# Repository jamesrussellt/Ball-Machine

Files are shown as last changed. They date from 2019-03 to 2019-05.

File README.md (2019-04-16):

# Ball-Sorting-Machine
University of Bath - Final Year Mechanical Engineering Masters Project

For exhibition and educational purposes.

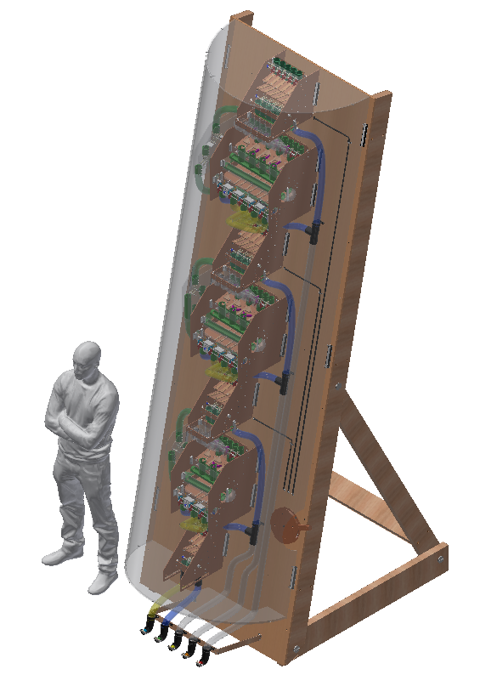
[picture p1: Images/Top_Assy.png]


## About this repository
As part of IMAGINARY open mathematics exhibitions (https://imaginary.org/), this machine demonstrates the use of Selection Sorting and Pancake Sorting Algorithms using balls of different weights.

## Selection Sorting Algorithm
This simple algorithm demonstrates the concept of sorting algorithms by least number of ball comparisons.

This algorithm picks the heaviest ball from the set of balls and places it to the right hand side of the pack. It will repeat this for the remaining balls until all balls have been sorted into weight order.

## Pancake Sorting Algorithm
This more complex algorithm demonstrates the concept of sorting algorithms by least number of reversals or 'flips'. You are more limited in this case than Selection Sort because you cannot simply pick the ball out of the pack and place it at the side.

Imagine you have a stack of pancakes of various sizes which you want in size order with the largest pancake (or heaviest ball in our case) at the bottom. You can only use your spatula to insert under the largest pancake and flip it, with any pancakes above it, so that the largest pancake rests on top of the pile. Then you re-insert your spatula at the bottom of the pile to flip all the pancakes at once so the largest pancake is now at the bottom of the pile. This method is repeated until all pancakes are in size order.

## How the machine works
The machine is effectively a repeat of a few sub assemblies which comprise the first line of the two algorithms. For each following line of both algorithms, the assemblies used are the same but adapted for one less ball lane.

A lever which can be seen towards the bottom right of the image above allows the user to switch between the two algorithms. For Selection Sort, the pancake comparator is skipped and the balls travel around it to the next selection comparator. For Pancake Sort, the balls travel straight from the selection comparator into the pancake comparator.

See `Pancake Sort` and `Selection Sort` for more information on how these comparators work to implement the two algorithms set out above.

## Contents

* `All Drawing PDFs`
  * All PDF manufacturing drawings for reference.
  * Drawings are also included in each sub-folder to show where they are used.
* `Top Level`
  * Machine full assembly.
  * Folder contains CAD models and manufacturing drawings.
* `Balls`
  * Balls of various weights required for the machine.
  * Folder contains CAD models and manufacturing drawings.
* `Pancake Sort`
  * Pancake Sort comparing mechanism.
  * Folder contains CAD models and manufacturing drawings.
* `Selection Sort`
  * Selection Sort comparing mechanism.
  * Folder contains CAD models and manufacturing drawings.
* `Timing Gate`
  * Timing Gate used for Selection Sort comparing mechanism.
  * Folder contains CAD models and manufacturing drawings.

The following folders were used for the creation of the machine and serve no purpose for manufacturing.

* `2018_Templates` 
  * Manufacturing drawing templates used when creating machine assembly and component drawings.
* `Images`
  * Images used for open source documentation.
* `Man`
  * CAD model of human used to present machine size.
* `OldVersions`
  * A backup of old overwritten files automatically saved when using Autodesk Inventor Software.
* `Prototype CAD`
  * A copy of the 'Selection Sort comparator' used to prove design principles.
  * Is built for larger 40mm balls and may contain other components for design adaptation.

## Manufacturing This Machine
Please see `BOM.xlsx` for full list of sub assemblies and parts required for this machine build.
Please see `All Drawing PDFs` for all manufacture drawings.

## Instructions 
See each folder for more detail.

## More info
Another comparing mechanism, designed by Evgeniy Shiryaev, can be used for sorting algorithms which require 2 balls to be compared at a time. This comparator was used as a starting point for the project and lead to the development of Selection and Pancake comparators which compare all balls at once.
See https://imaginary.org/hands-on/balls-sorting-mechanism

## Refer to this work
Cite as: James Taylor. (2019, March 28). jamesrussellt/Ball-Machine

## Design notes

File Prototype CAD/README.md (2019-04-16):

# Prototype CAD

A prototype of the `Selection Sort comparator` was made for demonstrating its design using larger 40mm balls.

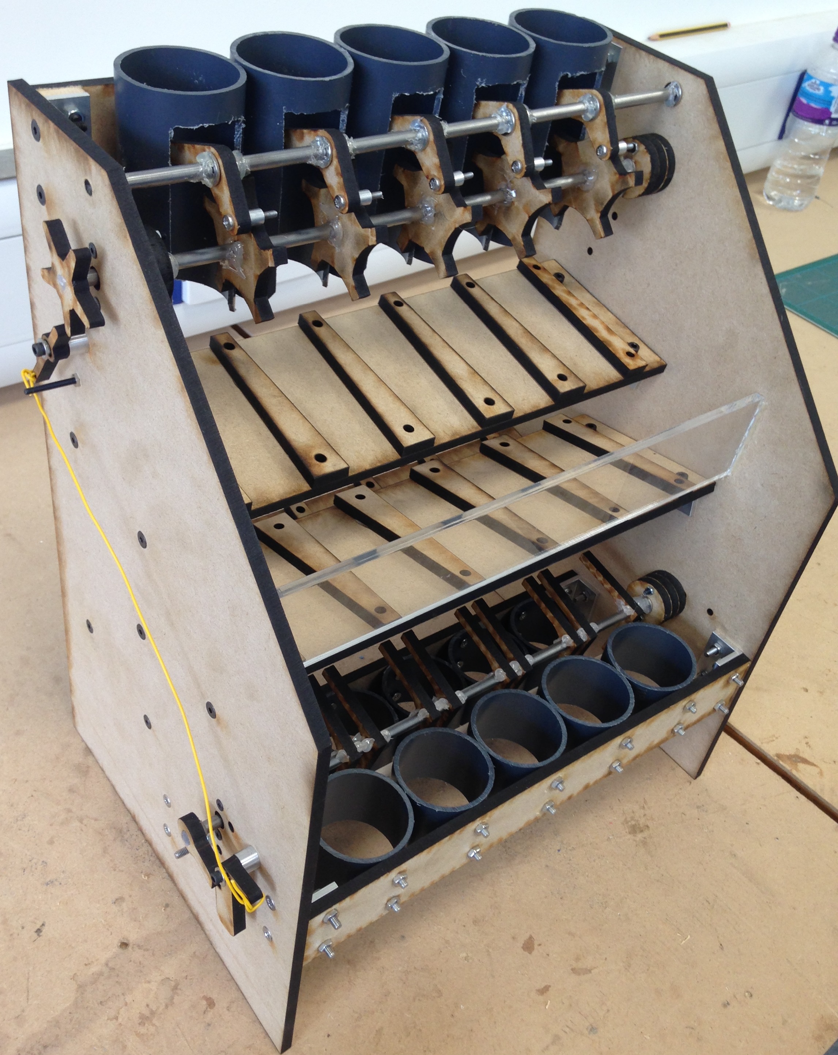
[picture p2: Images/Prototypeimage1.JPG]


Adaptations to the original design include:
 * A new `Star Piece` used in the `Timing Gate` assembly
 * A new `Reset Lever` used for holding and releasing the shaft used to separate the heaviest ball
 * A new `Ramp System` used for separating the heaviest ball from the rest

`Star Piece`
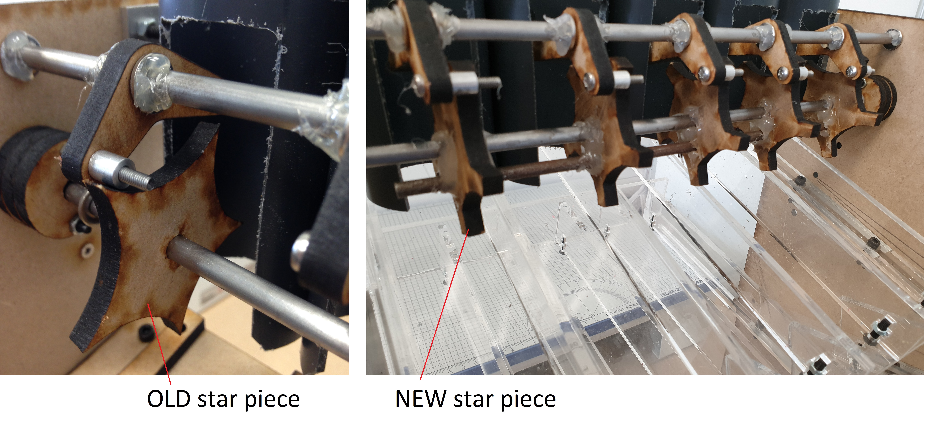
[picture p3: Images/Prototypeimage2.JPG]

 * Faces added to each point of star to prevent other lever slipping over it.

`Reset Lever`
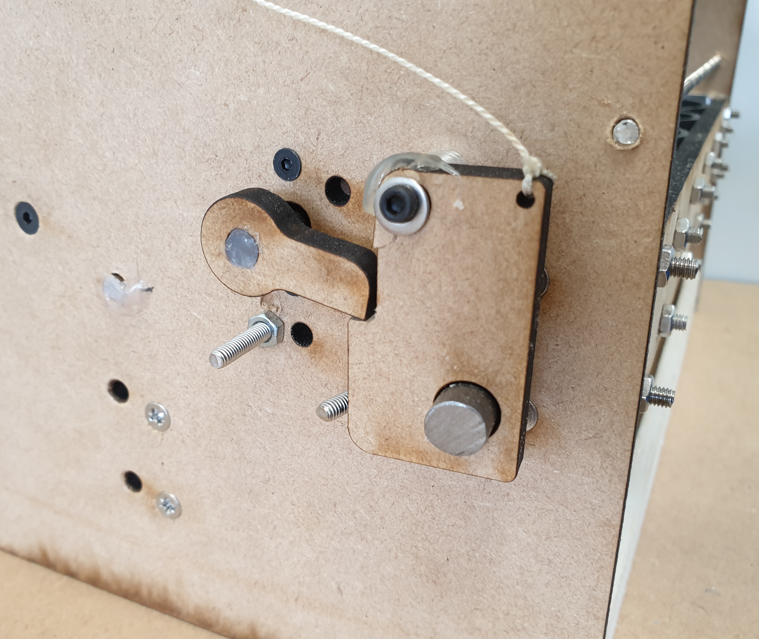
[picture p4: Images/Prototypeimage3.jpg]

 * Counter weight and stopper added to allow the lever to move into position faster when catching the shaft.
 * Please note lever was damaged in picture shown. Actual lever would not require glue to rest on shaft.

`Ramp System`
 * Old ramp system was proven by calculation and testing to not rely on ball weight but on ramp angle and friction. This design only works for balls of various surface roughnesses which may hinder starting speeds.
 * New ramp design required using individual rotating ramps per ball lane.
 * New ramp design has been calculated to require 3 rotating ramps of 150mm length each per ball lane.
 * This design will require further prototyping to prove its concept.

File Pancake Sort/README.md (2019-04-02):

# Pancake Sort

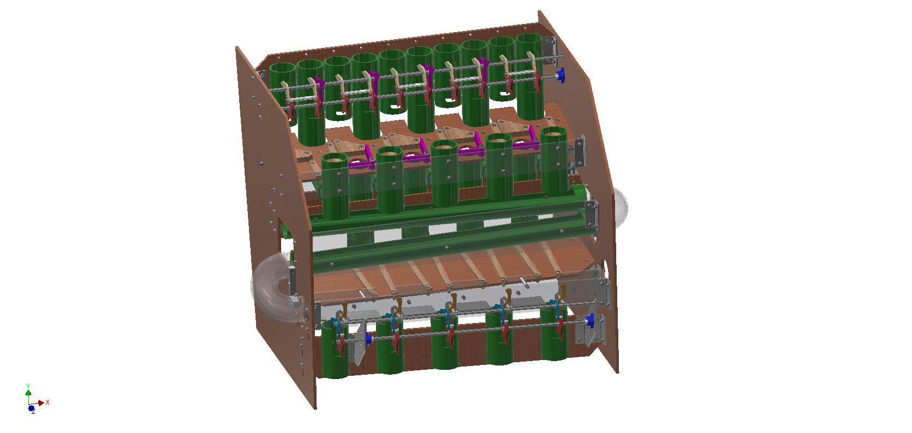
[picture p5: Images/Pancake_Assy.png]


This folder contains CAD models and drawings for the `Pancake Sort` comparator.

## How it works

This comparator uses the `Selection Sort` comparator before it to identify the heaviest ball and pass the balls into the corresponding `Pancake Sort` comparator entry tubes.

 * Each ball lane has two entry tubes (hence 10 entry tubes for 5 ball lanes) - Left for the lighter balls, Right for the heavier balls.

The `Pancake Sort` comparator flips the order of the heaviest ball and the balls to the left of it (just like flipping the largest pancake and all of the others on top of it). The balls to the right of the heaviest stay in lane. The tubes connecting the `Pancake Sort` comparator to the next line of the algorithm are connected so that the full sequence is flipped (the last stage of the Pancake Sort algorithm).

 * The heaviest ball hits a purple lever upon entry which changes the lane directions of the balls to the right of it.
 * These balls pass under the `Z` shaped ball run and into the exit timing gate.
 * The heaviest ball and the balls to the left pass into the `Z` shaped ball run.
 * This keeps the order of the balls the same as they pass into the exit timing gate.
 * The exit timing gate reverses the order of the entering balls as the first drops into place, the others pass over the top.
 * The balls are released out of the comparator at the same time for visual effect to watch the balls flip order as they pass through the connecting tubes (not shown in picture).

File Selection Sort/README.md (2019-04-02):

# Selection Sort

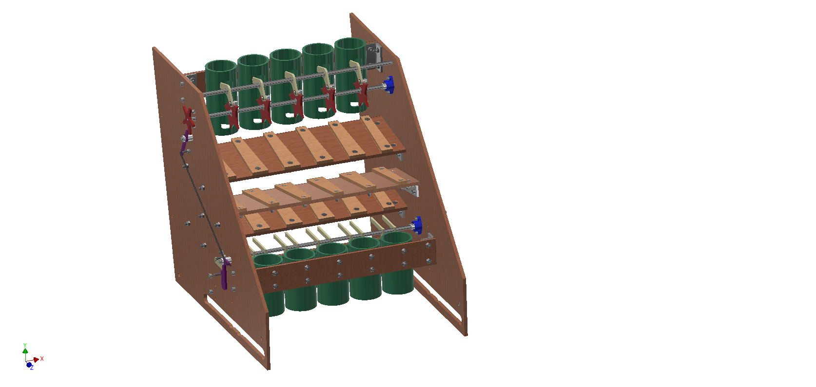
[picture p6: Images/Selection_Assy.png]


This folder contains the CAD models and manufacturing drawings required to make a selection sort comparator.

See folders `Selection - X Lanes` for copies of the design for the required number of ball lanes.

## How it works
The comparator is required to select and remove the heaviest ball as per the selection sort algorithm.

It comprises of 4 sections:
 * Timing Gate
 * Ramps
 * Selection Shaft
 * Reset mechanism
 
`Timing Gate`
 * To release all balls at the same time (see `Timing Gate` folder).
 
`Ramps`
* To allow the heaviest ball to roll to the bottom the quickest and separate it from the other balls (this design has been proven not to work and as such requires a design update and further prototyping work to complete - see `Prototype CAD` folder).
 
`Selection Shaft`
* The first ball down the ramps rotates the shaft and falls into the first set of tubes. The shaft is caught by a catch lever on the outer left hand side and the other balls roll over the top of the shaft into the other set of tubes. This separates the heaviest ball from the rest of the pack.

`Reset mechanism`
* For multiple uses of the machine, the reset mechanism releases the catch lever when the next set of balls pass the timing gate. A counterweight on the outer right hand side of the machine lifts the Selection shaft back into position.

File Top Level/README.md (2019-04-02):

# Top Level



This folder contains the full machine assembly using sub-assemblies from `Pancake Sort`, `Selection Sort` and `Timing Gate` along with manufacturing drawings.

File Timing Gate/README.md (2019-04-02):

# Timing Gate

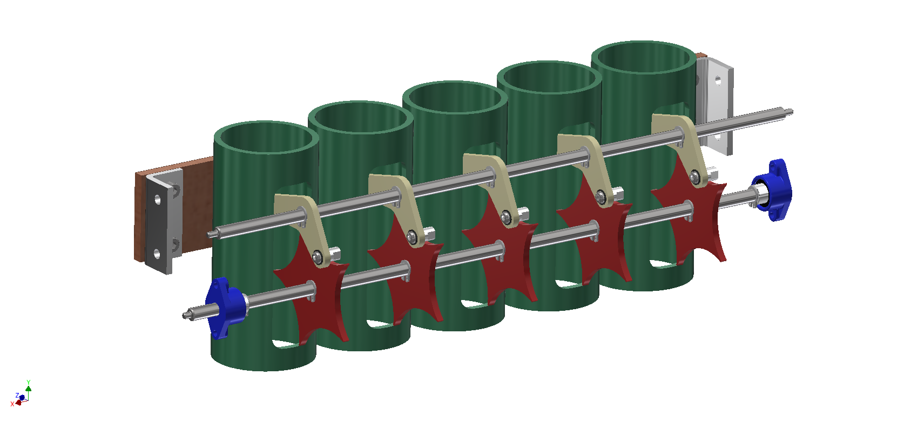
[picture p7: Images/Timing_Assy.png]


Used within `Selection Sort` comparator and adapated for the `Pancake Sort` comparator to release all balls at the same time once each ball arrives at the gate.

Each ball lifts the boomerange-shaped lever upon arrival which can rotate independantly on its shaft. Once all these levers are lifted, the star-shaped pieces, which are connected to the shaft so must rotate together, are free to rotate and the balls drop at the same time.

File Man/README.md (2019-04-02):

# Man

CAD model of human used to present machine size.

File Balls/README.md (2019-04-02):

# Balls

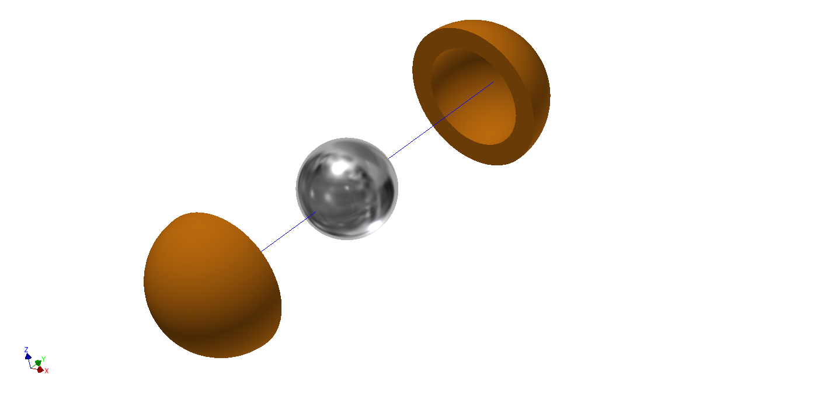
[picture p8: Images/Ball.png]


Contains models and drawings of balls to be used in machine.

Balls are made from steel ball bearings of various sizes incased in a 3D printed ABS plastic casing to ensure they all have the same outer diameter and surface roughness. The ball bearings are the main contributor in the weight difference between balls as steel has a high density of around 7700kg/m3.

The balls are manufactured from different coloured ABS plastic in the colours of the rainbow, i.e. red = heaviest ball -> blue = lightest ball. This allows people to see the balls sorted rather than having to compare weight differences by hand.

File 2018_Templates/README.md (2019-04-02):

# 2018_Templates

Manufacturing drawing templates used when creating machine assembly and component drawings (see image below).
Drawing template consists of premade borders and text boxes to increase productivity and consistency when creating part drawings.

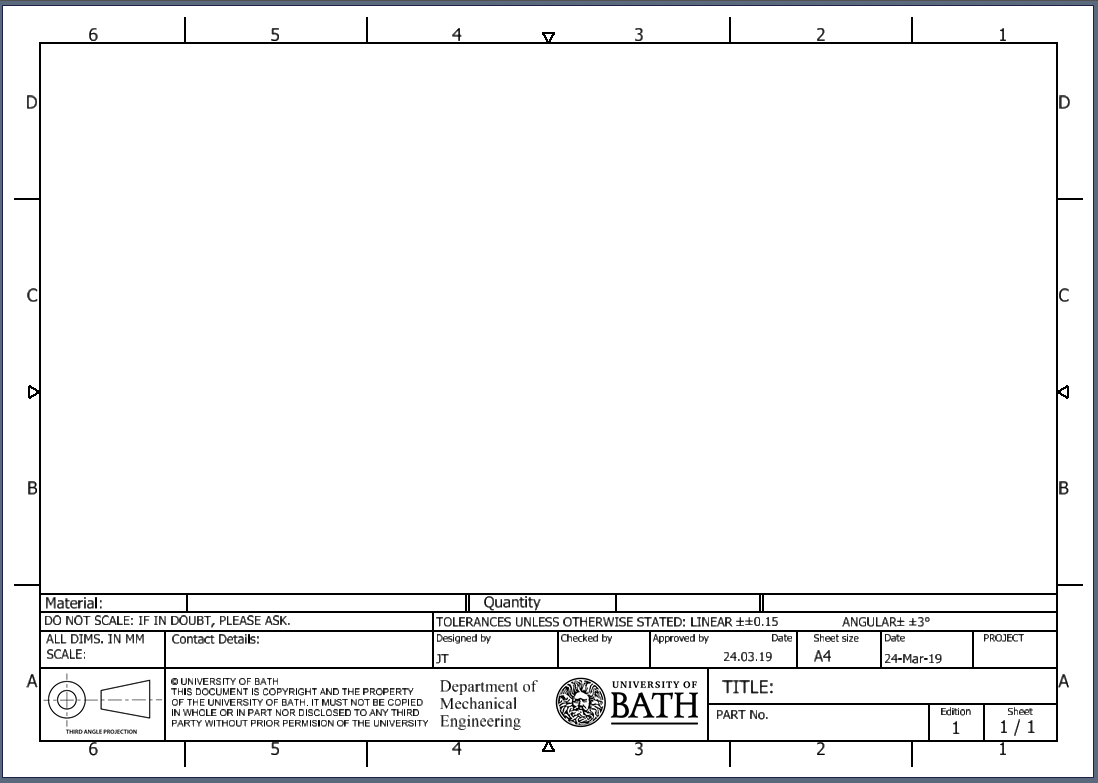
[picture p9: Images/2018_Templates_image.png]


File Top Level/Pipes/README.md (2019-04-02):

# Pipes

CAD models of all pipes used on `Top Level` assembly.

CAD models require multiple files for different pipe directions. In reality, flexible pipes will be cut from stock to length.

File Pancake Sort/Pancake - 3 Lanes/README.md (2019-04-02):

# Pancake Sort - 3 Lanes

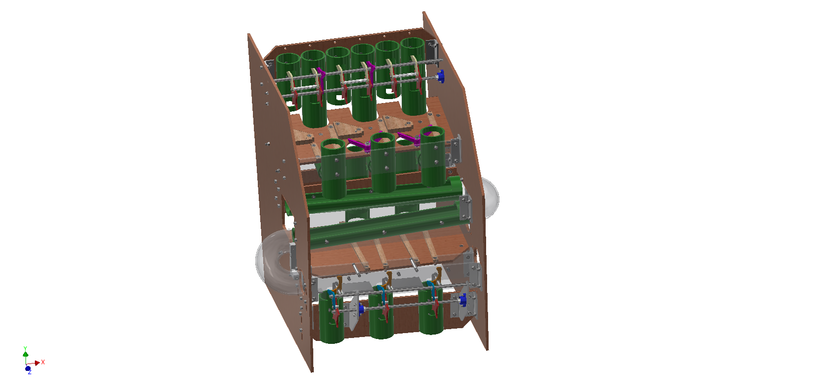
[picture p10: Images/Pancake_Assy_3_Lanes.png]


This folder is a copy of the Pancake Sort comparator design adapted for 3 ball lanes.

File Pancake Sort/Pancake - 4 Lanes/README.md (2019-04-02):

# Pancake Sort - 4 Lanes

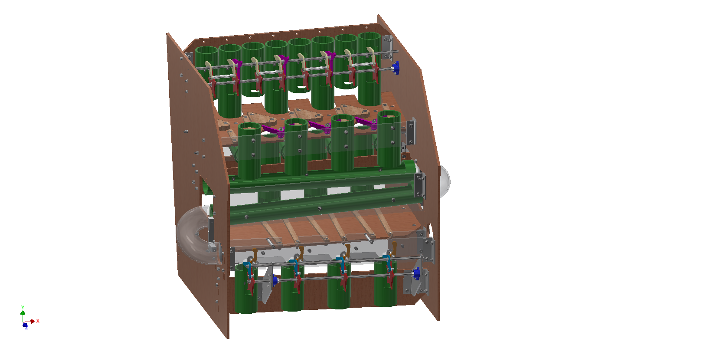
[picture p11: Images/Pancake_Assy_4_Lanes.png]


This folder is a copy of the Pancake Sort comparator design adapted for 4 ball lanes.

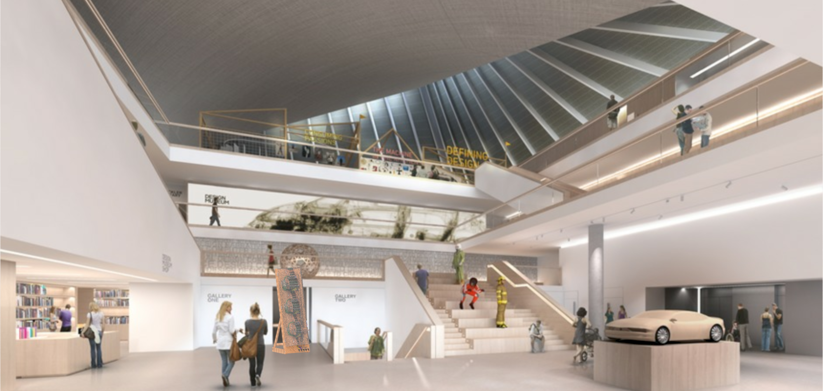
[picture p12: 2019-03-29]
Images/Top_Assy_Exhib_2.png

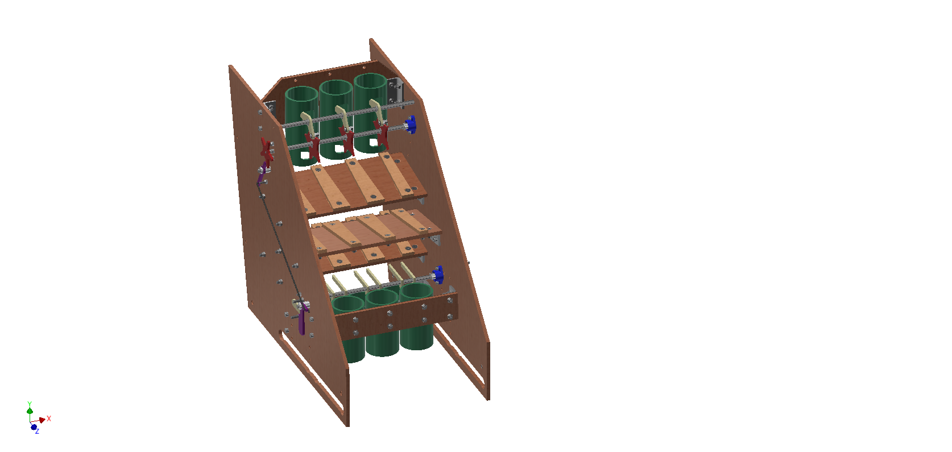
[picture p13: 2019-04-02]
Images/Selection_Assy_3_Lanes.png

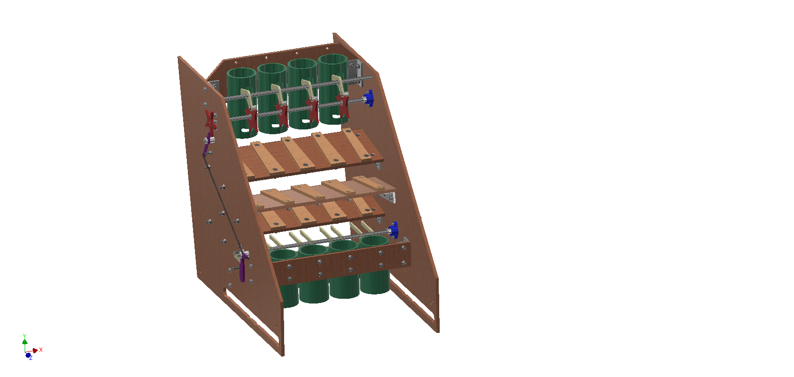
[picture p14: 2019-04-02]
Images/Selection_Assy_4_Lanes.png

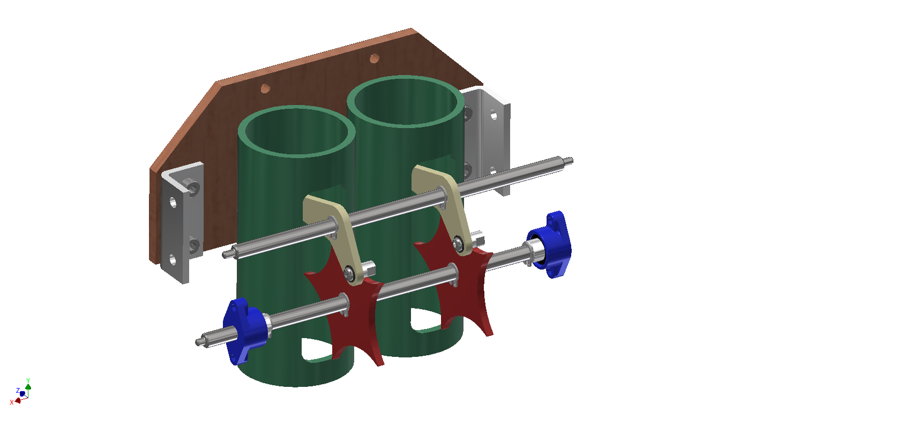
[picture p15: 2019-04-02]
Images/Timing_Assy_2_Lanes.png

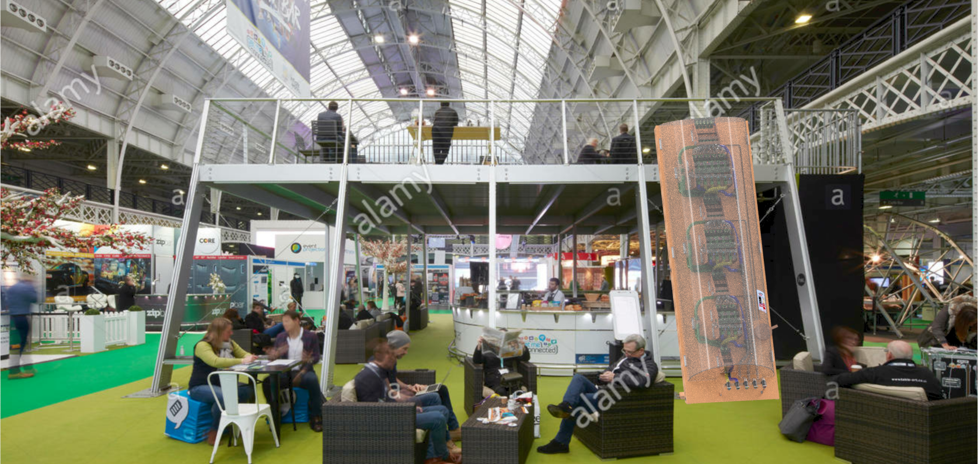
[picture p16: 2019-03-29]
Images/Top_Assy_Exhib_1.png

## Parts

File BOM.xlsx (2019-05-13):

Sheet: BOM
BOM
Top-Assy |  |  |  | Sub-Assy 1 |  |  |  | Sub-Assy 2 |  |  |  | Sub-Assy 3 |  |  |  | Sub-Assy 4
Part No. | Desc | Supplier | Qty | Part No. | Description | Supplier | Qty | Part No. | Description | Supplier | Qty | Part No. | Description | Supplier | Qty | Part No. | Description | Supplier | Qty
BSM.001.001 | Top_Assy | Workshop | 1 | 4082 | 42-50mm EPDM Adaptor | Plastic Pipe Shop | 34
 |  |  |  | 15528 | 40mm - 1 0.25inch Universal Plastic Pipe Clip c-w Spacer Block (PP) | Plastic Pipe Shop | 8
 |  |  |  | 16124 | 40mm Plain 90 Degree PVC Tee | Plastic Pipe Shop | 12
 |  |  |  | 450712010040016 | Socket Cap Screw - Standard - (A2) - M4 x 16 | TR Fastenings | 38
 |  |  |  | 450712010040025 | Socket Cap Screw - Standard - (A2) - M4 x 25 | TR Fastenings | 4
 |  |  |  | BSM.001.002 | Top_Backboard Assy | Workshop | 1 | 450712010040016 | Socket Cap Screw - Standard - (A2) - M4 x 16 | TR Fastenings | 52
 |  |  |  |  |  |  |  | 450712010040020 | Socket Cap Screw - Standard - (A2) - M4 x 20 | TR Fastenings | 12
 |  |  |  |  |  |  |  | 450712010040025 | Socket Cap Screw - Standard - (A2) - M4 x 25 | TR Fastenings | 40
 |  |  |  |  |  |  |  | 450712010080020 | Socket Cap Screw - Standard - (A2) - M8 x 20 | TR Fastenings | 6
 |  |  |  |  |  |  |  | BSM.001.103 | Top_Angle Bracket | Workshop | 26
 |  |  |  |  |  |  |  | BSM.001.104 | Top_Backboard | Workshop | 1
 |  |  |  |  |  |  |  | BSM.001.112 | Top_Floor Plank | Workshop | 2
 |  |  |  |  |  |  |  | BSM.001.116 | Top_Hinge Cylinder Long | Workshop | 2
 |  |  |  |  |  |  |  | BSM.001.117 | Top_Hinge Cylinder | Workshop | 4
 |  |  |  |  |  |  |  | BSM.001.118 | Top_Hinge End | Workshop | 6
 |  |  |  |  |  |  |  | BSM.001.126 | Top_Rear Plank_LHS | Workshop | 1
 |  |  |  |  |  |  |  | BSM.001.127 | Top_Rear Plank_RHS | Workshop | 1
 |  |  |  |  |  |  |  | BSM.001.128 | Top_Reinforcement 2 | Workshop | 3
 |  |  |  |  |  |  |  | BSM.001.129 | Top_Reinforcement 3 | Workshop | 1
 |  |  |  |  |  |  |  | BSM.001.130 | Top_Reinforcement_LHS | Workshop | 1
 |  |  |  |  |  |  |  | BSM.001.131 | Top_Reinforcement_RHS | Workshop | 1
 |  |  |  |  |  |  |  | BSM.001.148 | Top_Spacer | Workshop | 2
 |  |  |  |  |  |  |  | Din97 - 4x25 | Steel Wood Screw |  | 29
 |  |  |  |  |  |  |  | Din97 - 8x80 | Steel Wood Screw |  | 24
 |  |  |  |  |  |  |  | M4 - Nyloc Nut | Nyloc Nut - M4 | TR Fastenings | 92
 |  |  |  | BSM.001.003 | Top_Lever Assy | Workshop | 1 | 450712010080030 | Socket Cap Screw - Standard - (A2) - M8 x 30 | TR Fastenings | 1
 |  |  |  |  |  |  |  | BSM.001.119 | Top_Lever 2mm Spacer | Workshop | 1
 |  |  |  |  |  |  |  | BSM.001.120 | Top_Lever Cable Tie | Workshop | 6
 |  |  |  |  |  |  |  | BSM.001.121 | Top_Lever Centre | Workshop | 1
 |  |  |  |  |  |  |  | BSM.001.122 | Top_Lever End Piece | Workshop | 1
 |  |  |  |  |  |  |  | BSM.001.123 | Top_Lever Handle | Workshop | 1
 |  |  |  |  |  |  |  | BSM.001.124 | Top_Lever Shaft | Workshop | 1
 |  |  |  |  |  |  |  | BSM.001.125 | Top_Lever Side | Workshop | 2
 |  |  |  |  |  |  |  | Din97 - 4x12 | Steel Wood Screw |  | 18
 |  |  |  |  |  |  |  | M4 x 12 - Socket Csk Screw (A2) | Socket Csk Screw - (A2) - M4 x 12 | TR Fastenings | 1
 |  |  |  |  |  |  |  | PRB-256 | Standard Double Sealed Ball Bearing | SKF | 2
 |  |  |  | BSM.001.004 | Top_Separator Assy 2 Lanes | Workshop | 1 | 450712010040016 | Socket Cap Screw - Standard - (A2) - M4 x 16 | TR Fastenings | 4
 |  |  |  |  |  |  |  | 450712010040025 | Socket Cap Screw - Standard - (A2) - M4 x 25 | TR Fastenings | 4
 |  |  |  |  |  |  |  | BSM.001.103 | Top_Angle Bracket | Workshop | 2
 |  |  |  |  |  |  |  | BSM.001.132 | Top_Separator Backboard 2 Lanes | Workshop | 2
 |  |  |  |  |  |  |  | BSM.001.136 | Top_Separator Lever | Workshop | 2
 |  |  |  |  |  |  |  | BSM.001.138 | Top_Separator Pipe | Workshop | 3
 |  |  |  |  |  |  |  | BSM.001.139 | Top_Separator Shaft | Workshop | 1
 |  |  |  |  |  |  |  | BSM.001.140 | Top_Separator Weight 2 | Workshop | 2
 |  |  |  |  |  |  |  | BSM.001.141 | Top_Separator Weight | Workshop | 1
 |  |  |  |  |  |  |  | BSM.004.102 | Pancake_Bearing | Workshop | 2
 |  |  |  |  |  |  |  | circlip-6-bs-3673 | External Circlip |  | 2
 |  |  |  |  |  |  |  | M3 x 8 - Socket Cap Screw - Standard (A2) | Socket Cap Screw - Standard - (A2) - M3 x 8 | TR Fastenings | 6
 |  |  |  |  |  |  |  | M4 - Nyloc Nut | Nyloc Nut - M4 | TR Fastenings | 14
 |  |  |  |  |  |  |  | M4 x 16 - Socket Csk Screw (A2) | Socket Csk Screw - (A2) - M4 x 16 | TR Fastenings | 6
 |  |  |  | BSM.001.005 | Top_Separator Assy 3 Lanes | Workshop | 1 | 450712010040016 | Socket Cap Screw - Standard - (A2) - M4 x 16 | TR Fastenings | 4
 |  |  |  |  |  |  |  | 450712010040025 | Socket Cap Screw - Standard - (A2) - M4 x 25 | TR Fastenings | 4
 |  |  |  |  |  |  |  | BSM.001.103 | Top_Angle Bracket | Workshop | 2
 |  |  |  |  |  |  |  | BSM.001.133 | Top_Separator Backboard 3 Lanes | Workshop | 2
 |  |  |  |  |  |  |  | BSM.001.136 | Top_Separator Lever | Workshop | 4
 |  |  |  |  |  |  |  | BSM.001.137 | Top_Separator Pipe Long | Workshop | 1
 |  |  |  |  |  |  |  | BSM.001.138 | Top_Separator Pipe | Workshop | 4
 |  |  |  |  |  |  |  | BSM.001.139 | Top_Separator Shaft | Workshop | 2
 |  |  |  |  |  |  |  | BSM.001.140 | Top_Separator Weight 2 | Workshop | 4
 |  |  |  |  |  |  |  | BSM.001.141 | Top_Separator Weight | Workshop | 2
 |  |  |  |  |  |  |  | BSM.004.102 | Pancake_Bearing | Workshop | 4
 |  |  |  |  |  |  |  | circlip-6-bs-3673 | External Circlip |  | 4
 |  |  |  |  |  |  |  | M3 x 8 - Socket Cap Screw - Standard (A2) | Socket Cap Screw - Standard - (A2) - M3 x 8 | TR Fastenings | 12
 |  |  |  |  |  |  |  | M4 - Nyloc Nut | Nyloc Nut - M4 | TR Fastenings | 18
 |  |  |  |  |  |  |  | M4 x 16 - Socket Csk Screw (A2) | Socket Csk Screw - (A2) - M4 x 16 | TR Fastenings | 10
 |  |  |  | BSM.001.006 | Top_Separator Assy | Workshop | 1 | 450712010040016 | Socket Cap Screw - Standard - (A2) - M4 x 16 | TR Fastenings | 4
 |  |  |  |  |  |  |  | 450712010040025 | Socket Cap Screw - Standard - (A2) - M4 x 25 | TR Fastenings | 4
 |  |  |  |  |  |  |  | BSM.001.103 | Top_Angle Bracket | Workshop | 2
 |  |  |  |  |  |  |  | BSM.001.134 | Top_Separator Backboard | Workshop | 2
 |  |  |  |  |  |  |  | BSM.001.135 | Top_Separator Block | Workshop | 2
 |  |  |  |  |  |  |  | BSM.001.136 | Top_Separator Lever | Workshop | 6
 |  |  |  |  |  |  |  | BSM.001.138 | Top_Separator Pipe | Workshop | 7
 |  |  |  |  |  |  |  | BSM.001.139 | Top_Separator Shaft | Workshop | 3
 |  |  |  |  |  |  |  | BSM.001.140 | Top_Separator Weight 2 | Workshop | 6
 |  |  |  |  |  |  |  | BSM.001.141 | Top_Separator Weight | Workshop | 3
 |  |  |  |  |  |  |  | BSM.004.102 | Pancake_Bearing | Workshop | 6
 |  |  |  |  |  |  |  | circlip-6-bs-3673 | External Circlip |  | 6
 |  |  |  |  |  |  |  | M3 x 8 - Socket Cap Screw - Standard (A2) | Socket Cap Screw - Standard - (A2) - M3 x 8 | TR Fastenings | 26
 |  |  |  |  |  |  |  | M4 - Nyloc Nut | Nyloc Nut - M4 | TR Fastenings | 22
 |  |  |  |  |  |  |  | M4 x 16 - Socket Csk Screw (A2) | Socket Csk Screw - (A2) - M4 x 16 | TR Fastenings | 14
 |  |  |  | BSM.001.007 | Top_Slider Assy | Workshop | 1 | 618-6 SKF | Deep Groove Ball Bearing | SKF | 4
 |  |  |  |  |  |  |  | 450712010040016 | Socket Cap Screw - Standard - (A2) - M4 x 16 | TR Fastenings | 12
 |  |  |  |  |  |  |  | 451233010040020 | Socket Csk Screw - (A2) - M4 x 20 | TR Fastenings | 4
 |  |  |  |  |  |  |  | BSM.001.100 | Top_6mm Spacer | Workshop | 4
 |  |  |  |  |  |  |  | BSM.001.142 | Top_Shaft 1 | Workshop | 4
 |  |  |  |  |  |  |  | BSM.001.143 | Top_Slider Piece 1 | Workshop | 3
 |  |  |  |  |  |  |  | BSM.001.146 | Top_Slider Piece 2 | Workshop | 1
 |  |  |  |  |  |  |  | BSM.001.147 | Top_Slider Piece 3 | Workshop | 1
 |  |  |  |  |  |  |  | BSM.001.149 | Top_Tilt Pipe | Workshop | 2
 |  |  |  |  |  |  |  | BSM.001.152 | Top_Pipe 01 | Workshop | 10
 |  |  |  |  |  |  |  | BSM.002.115 | Selection_Washer | Workshop | 4
 |  |  |  |  |  |  |  | BSM.003.100 | Timing_Angle Bracket | Workshop | 6
 |  |  |  |  |  |  |  | M3 x 5 - Socket Cap Screw - Standard (A2) | Socket Cap Screw - Standard - (A2) - M3 x 5 | TR Fastenings | 4
 |  |  |  |  |  |  |  | M3 x 8 - Socket Cap Screw - Standard (A2) | Socket Cap Screw - Standard - (A2) - M3 x 8 | TR Fastenings | 4
 |  |  |  |  |  |  |  | M4 - Nyloc Nut | Nyloc Nut - M4 | TR Fastenings | 48
 |  |  |  |  |  |  |  | M4 x 12 - Socket Csk Screw (A2) | Socket Csk Screw - (A2) - M4 x 12 | TR Fastenings | 12
 |  |  |  |  |  |  |  | M4 x 16 - Socket Csk Screw (A2) | Socket Csk Screw - (A2) - M4 x 16 | TR Fastenings | 20
 |  |  |  | BSM.001.008 | Top_Slider Assy_3 Lanes | Workshop | 1 | 618-6 SKF | Deep Groove Ball Bearing | SKF | 4
 |  |  |  |  |  |  |  | 450712010040016 | Socket Cap Screw - Standard - (A2) - M4 x 16 | TR Fastenings | 12
 |  |  |  |  |  |  |  | 451233010040020 | Socket Csk Screw - (A2) - M4 x 20 | TR Fastenings | 4
 |  |  |  |  |  |  |  | BSM.001.100 | Top_6mm Spacer | Workshop | 4
 |  |  |  |  |  |  |  | BSM.001.142 | Top_Shaft 1 | Workshop | 4
 |  |  |  |  |  |  |  | BSM.001.144 | Top_Slider Piece 1_3 Lanes | Workshop | 3
 |  |  |  |  |  |  |  | BSM.001.146 | Top_Slider Piece 2 | Workshop | 1
 |  |  |  |  |  |  |  | BSM.001.147 | Top_Slider Piece 3 | Workshop | 1
 |  |  |  |  |  |  |  | BSM.001.150 | Top_Tilt Pipe_3 Lanes | Workshop | 2
 |  |  |  |  |  |  |  | BSM.001.152 | Top_Pipe 01 | Workshop | 6
 |  |  |  |  |  |  |  | BSM.002.115 | Selection_Washer | Workshop | 4
 |  |  |  |  |  |  |  | BSM.003.100 | Timing_Angle Bracket | Workshop | 6
 |  |  |  |  |  |  |  | M3 x 5 - Socket Cap Screw - Standard (A2) | Socket Cap Screw - Standard - (A2) - M3 x 5 | TR Fastenings | 4
 |  |  |  |  |  |  |  | M3 x 8 - Socket Cap Screw - Standard (A2) | Socket Cap Screw - Standard - (A2) - M3 x 8 | TR Fastenings | 4
 |  |  |  |  |  |  |  | M4 - Nyloc Nut | Nyloc Nut - M4 | TR Fastenings | 40
 |  |  |  |  |  |  |  | M4 x 12 - Socket Csk Screw (A2) | Socket Csk Screw - (A2) - M4 x 12 | TR Fastenings | 12
 |  |  |  |  |  |  |  | M4 x 16 - Socket Csk Screw (A2) | Socket Csk Screw - (A2) - M4 x 16 | TR Fastenings | 12
 |  |  |  | BSM.001.009 | Top_Slider Assy_4 Lanes | Workshop | 1 | 618-6 SKF | Deep Groove Ball Bearing | SKF | 4
 |  |  |  |  |  |  |  | 450712010040016 | Socket Cap Screw - Standard - (A2) - M4 x 16 | TR Fastenings | 12
 |  |  |  |  |  |  |  | 451233010040020 | Socket Csk Screw - (A2) - M4 x 20 | TR Fastenings | 4
 |  |  |  |  |  |  |  | BSM.001.100 | Top_6mm Spacer | Workshop | 4
 |  |  |  |  |  |  |  | BSM.001.142 | Top_Shaft 1 | Workshop | 4
 |  |  |  |  |  |  |  | BSM.001.145 | Top_Slider Piece 1_4 Lanes | Workshop | 3
 |  |  |  |  |  |  |  | BSM.001.146 | Top_Slider Piece 2 | Workshop | 1
 |  |  |  |  |  |  |  | BSM.001.147 | Top_Slider Piece 3 | Workshop | 1
 |  |  |  |  |  |  |  | BSM.001.151 | Top_Tilt Pipe_4 Lanes | Workshop | 2
 |  |  |  |  |  |  |  | BSM.001.152 | Top_Pipe 01 | Workshop | 8
 |  |  |  |  |  |  |  | BSM.002.115 | Selection_Washer | Workshop | 4
 |  |  |  |  |  |  |  | BSM.003.100 | Timing_Angle Bracket | Workshop | 6
 |  |  |  |  |  |  |  | M3 x 5 - Socket Cap Screw - Standard (A2) | Socket Cap Screw - Standard - (A2) - M3 x 5 | TR Fastenings | 4
 |  |  |  |  |  |  |  | M3 x 8 - Socket Cap Screw - Standard (A2) | Socket Cap Screw - Standard - (A2) - M3 x 8 | TR Fastenings | 4
 |  |  |  |  |  |  |  | M4 - Nyloc Nut | Nyloc Nut - M4 | TR Fastenings | 44
 |  |  |  |  |  |  |  | M4 x 12 - Socket Csk Screw (A2) | Socket Csk Screw - (A2) - M4 x 12 | TR Fastenings | 12
 |  |  |  |  |  |  |  | M4 x 16 - Socket Csk Screw (A2) | Socket Csk Screw - (A2) - M4 x 16 | TR Fastenings | 16
 |  |  |  | BSM.001.101 | Top_45 Deg Connector | Workshop | 2
 |  |  |  | BSM.001.102 | Top_Angle Bracket Small | Workshop | 6
 |  |  |  | BSM.001.105 | Top_Cable End | Workshop | 6
 |  |  |  | BSM.001.106 | Top_Cable Tie | Workshop | 3
 |  |  |  | BSM.001.107 | Top_End Piece 1 | Workshop | 2
 |  |  |  | BSM.001.108 | Top_End Piece 2 | Workshop | 1
 |  |  |  | BSM.001.109 | Top_End Pipe | Workshop | 5
 |  |  |  | BSM.001.110 | Top_End Sponge | Workshop | 5
 |  |  |  | BSM.001.111 | Top_End Stopper | Workshop | 5
 |  |  |  | BSM.001.113 | Top_Guard 1 | Workshop | 1
 |  |  |  | BSM.001.114 | Top_Guard 2 | Workshop | 1
 |  |  |  | BSM.001.115 | Top_Guard 3 | Workshop | 1
 |  |  |  | BSM.001.152 | Top_Pipe 01 | Workshop | 1
 |  |  |  | BSM.001.153 | Top_Cable 01 | Workshop | 1
 |  |  |  | BSM.003.100 | Timing_Angle Bracket | Workshop | 4
 |  |  |  | M3 x 12 - Socket Csk Screw (A2) | Socket Csk Screw - (A2) - M3 x 12 | TR Fastenings | 10
 |  |  |  | M3 x 16 - Socket Csk Screw (A2) | Socket Csk Screw - (A2) - M3 x 16 | TR Fastenings | 10
 |  |  |  | M3 x 25 - Socket Cap Screw - Standard (A2) | Socket Cap Screw - Standard - (A2) - M3 x 25 | TR Fastenings | 28
 |  |  |  | M4 - Nyloc Nut | Nyloc Nut - M4 | TR Fastenings | 71
 |  |  |  | M4 x 16 - Socket Csk Screw (A2) | Socket Csk Screw - (A2) - M4 x 16 | TR Fastenings | 43
 |  |  |  | nut_din_985-m3x0_5-8 | M3 Locknut | TR Fastenings | 48
 |  |  |  | BSM.002.001 | Selection_Assy |  | 1 | 450712010040016 | Socket Cap Screw - Standard - (A2) - M4 x 16 | TR Fastenings | 24
 |  |  |  |  |  |  |  | 450712010040020 | Socket Cap Screw - Standard - (A2) - M4 x 20 | TR Fastenings | 2
 |  |  |  |  |  |  |  | BSM.002.002 | Selection_Exit Pipe Assy | Workshop | 1 | 450712010040016 | Socket Cap Screw - Standard - (A2) - M4 x 16 | TR Fastenings | 4
 |  |  |  |  |  |  |  |  |  |  |  | BSM.002.102 | Selection_Exit Pipe | Workshop | 5
 |  |  |  |  |  |  |  |  |  |  |  | BSM.003.100 | Timing_Angle Bracket | Workshop | 2
 |  |  |  |  |  |  |  |  |  |  |  | BSM.003.101 | Timing_Backboard | Workshop | 1
 |  |  |  |  |  |  |  |  |  |  |  | M4 - Nyloc Nut | Nyloc Nut - M4 | TR Fastenings | 14
 |  |  |  |  |  |  |  |  |  |  |  | M4 x 16 - Socket Csk Screw (A2) | Socket Csk Screw - (A2) - M4 x 16 | TR Fastenings | 10
 |  |  |  |  |  |  |  | BSM.002.003 | Selection_Ramp 1 | Workshop | 3 | BSM.002.100 | Selection_Angle Bracket 1 | Workshop | 2
 |  |  |  |  |  |  |  |  |  |  |  | BSM.002.109 | Selection_Ramp 1 | Workshop | 1
 |  |  |  |  |  |  |  |  |  |  |  | BSM.002.110 | Selection_Ramp 1_LHS Piece | Workshop | 1
 |  |  |  |  |  |  |  |  |  |  |  | BSM.002.111 | Selection_Ramp 1_Mid piece | Workshop | 4
 |  |  |  |  |  |  |  |  |  |  |  | BSM.002.112 | Selection_Ramp 1_RHS Piece | Workshop | 1
 |  |  |  |  |  |  |  |  |  |  |  | M4 - Nyloc Nut | Nyloc Nut - M4 | TR Fastenings | 16
 |  |  |  |  |  |  |  |  |  |  |  | M4 x 12 - Socket Csk Screw (A2) | Socket Csk Screw - (A2) - M4 x 12 | TR Fastenings | 4
 |  |  |  |  |  |  |  |  |  |  |  | M4 x 16 - Socket Csk Screw (A2) | Socket Csk Screw - (A2) - M4 x 16 | TR Fastenings | 12
 |  |  |  |  |  |  |  | BSM.002.004 | Selection_Shaft Assy | Workshop | 1 | BSM.002.113 | Selection_Selector 1 | Workshop | 10
 |  |  |  |  |  |  |  |  |  |  |  | BSM.002.114 | Selection_Shaft 1 | Workshop | 1
 |  |  |  |  |  |  |  |  |  |  |  | circlip-6-bs-3673 | External Circlip | TR Fastenings | 12
 |  |  |  |  |  |  |  | BSM.002.005 | Selection_Exit Pipe Assy Long | Workshop | 1 | 450712010040016 | Socket Cap Screw - Standard - (A2) - M4 x 16 | TR Fastenings | 4
 |  |  |  |  |  |  |  |  |  |  |  | BSM.002.118 | Selection_Exit Pipe Long | Workshop | 5
 |  |  |  |  |  |  |  |  |  |  |  | BSM.003.100 | Timing_Angle Bracket | Workshop | 2
 |  |  |  |  |  |  |  |  |  |  |  | BSM.003.101 | Timing_Backboard | Workshop | 1
 |  |  |  |  |  |  |  |  |  |  |  | M4 - Nyloc Nut | Nyloc Nut - M4 | TR Fastenings | 14
 |  |  |  |  |  |  |  |  |  |  |  | M4 x 16 - Socket Csk Screw (A2) | Socket Csk Screw - (A2) - M4 x 16 | TR Fastenings | 10
 |  |  |  |  |  |  |  | BSM.002.101 | Selection_Counterweight | Workshop | 1
 |  |  |  |  |  |  |  | BSM.002.103 | Selection_Gear 1 | Workshop | 1
 |  |  |  |  |  |  |  | BSM.002.104 | Selection_Lever 1 | Workshop | 1
 |  |  |  |  |  |  |  | BSM.002.105 | Selection_Lever 2 | Workshop | 1
 |  |  |  |  |  |  |  | BSM.002.106 | Selection_Lever 3 | Workshop | 1
 |  |  |  |  |  |  |  | BSM.002.107 | Selection_Lever Mount Piece | Workshop | 2
 |  |  |  |  |  |  |  | BSM.002.108 | Selection_LHS | Workshop | 2
 |  |  |  |  |  |  |  | BSM.002.115 | Selection_Washer | Workshop | 2
 |  |  |  |  |  |  |  | BSM.002.116 | Selection_Weight | Workshop | 4
 |  |  |  |  |  |  |  | BSM.002.117 | Selection_Wire | Workshop | 1
 |  |  |  |  |  |  |  | BSM.003.001 | Timing_Assy | Workshop | 1 | 450712010040016 | Socket Cap Screw - Standard - (A2) - M4 x 16 | TR Fastenings | 4
 |  |  |  |  |  |  |  |  |  |  |  | BSM.003.002 | Timing_Assy_Lever Shaft | Workshop | 1 | BSM.003.102 | Timing_Lever Shaft | Workshop | 1
 |  |  |  |  |  |  |  |  |  |  |  |  |  |  |  | BSM.003.103 | Timing_Lever Weight | Workshop | 5
 |  |  |  |  |  |  |  |  |  |  |  |  |  |  |  | BSM.003.104 | Timing_Lever | Workshop | 5
 |  |  |  |  |  |  |  |  |  |  |  |  |  |  |  | circlip-6-bs-3673 | External Circlip | TR Fastenings | 10
 |  |  |  |  |  |  |  |  |  |  |  |  |  |  |  | M3 x 0.5mm Zinc Plated Steel Washer | M3 x 0.5mm Zinc Plated Steel Washer | TR Fastenings | 5
 |  |  |  |  |  |  |  |  |  |  |  |  |  |  |  | M3 x 10 - Socket Button Head (A2) | Socket Button Head - (A2) - M3 x 10 | TR Fastenings | 5
 |  |  |  |  |  |  |  |  |  |  |  | BSM.003.003 | Timing_Assy_Star Shaft | Workshop | 1 | BSM.003.106 | Timing_Star Shaft | Workshop | 1
 |  |  |  |  |  |  |  |  |  |  |  |  |  |  |  | BSM.003.107 | Timing_Star | Workshop | 5
 |  |  |  |  |  |  |  |  |  |  |  |  |  |  |  | circlip-6-bs-3673 | External Circlip | TR Fastenings | 7
 |  |  |  |  |  |  |  |  |  |  |  |  |  |  |  | SAFL212 | Oval 2 Bolt Flanged Unit | TR Fastenings | 2
 |  |  |  |  |  |  |  |  |  |  |  | BSM.003.100 | Timing_Angle Bracket | Workshop | 2
 |  |  |  |  |  |  |  |  |  |  |  | BSM.003.101 | Timing_Backboard | Workshop | 1
 |  |  |  |  |  |  |  |  |  |  |  | BSM.003.105 | Timing_PVC Pipe | Workshop | 5
 |  |  |  |  |  |  |  |  |  |  |  | M4 - Nyloc Nut | Nyloc Nut - M4 | TR Fastenings | 14
 |  |  |  |  |  |  |  |  |  |  |  | M4 x 16 - Socket Csk Screw (A2) | Socket Csk Screw - (A2) - M4 x 16 | TR Fastenings | 10
 |  |  |  |  |  |  |  | BSM.004.102 | Pancake_Bearing | Workshop | 2
 |  |  |  |  |  |  |  | M3 x 8 - Socket Cap Screw - Standard (A2) | Socket Cap Screw - Standard - (A2) - M3 x 8 | TR Fastenings | 4
 |  |  |  |  |  |  |  | M3 x 10 - Hex. Head Set Screw (MS) | Hex. Head Set Screw (MS) - M3 x 10 | TR Fastenings | 1
 |  |  |  |  |  |  |  | M3 x 16 - Socket Cap Screw - Standard (A2) | Socket Cap Screw - Standard - (A2) - M3 x 16 | TR Fastenings | 9
 |  |  |  |  |  |  |  | M4 - Nyloc Nut | Nyloc Nut - M4 | TR Fastenings | 26
 |  |  |  |  |  |  |  | nut_din_985-m3x0_5-8 | M3 Locknut | TR Fastenings | 10
 |  |  |  |  |  |  |  | SAFL212 | Oval 2 Bolt Flanged Unit | acorn | 2
 |  |  |  | BSM.004.001 | Pancake_Assy | Workshop | 1 | 450712010040016 | Socket Cap Screw - Standard - (A2) - M4 x 16 | TR Fastenings | 22
 |  |  |  |  |  |  |  | BSM.004.002 | Pancake_Catch Assy | Workshop | 2 | 450712010040016 | Socket Cap Screw - Standard - (A2) - M4 x 16 | TR Fastenings | 4
 |  |  |  |  |  |  |  |  |  |  |  | BSM.004.101 | Pancake_Angle Bracket | Workshop | 2
 |  |  |  |  |  |  |  |  |  |  |  | BSM.004.104 | Pancake_Catch Backboard | Workshop | 1
 |  |  |  |  |  |  |  |  |  |  |  | BSM.004.105 | Pancake_Catch Pipe | Workshop | 5
 |  |  |  |  |  |  |  |  |  |  |  | M4 - Nyloc Nut | Nyloc Nut - M4 | TR Fastenings | 14
 |  |  |  |  |  |  |  |  |  |  |  | M4 x 16 - Socket Csk Screw (A2) | Socket Csk Screw - (A2) - M4 x 16 | TR Fastenings | 10
 |  |  |  |  |  |  |  | BSM.004.003 | Pancake_Drop Assy | Workshop | 1 | 450712010040016 | Socket Cap Screw - Standard - (A2) - M4 x 16 | TR Fastenings | 4
 |  |  |  |  |  |  |  |  |  |  |  | BSM.004.101 | Pancake_Angle Bracket | Workshop | 2
 |  |  |  |  |  |  |  |  |  |  |  | BSM.004.107 | Pancake_Drop Backboard | Workshop | 1
 |  |  |  |  |  |  |  |  |  |  |  | BSM.004.108 | Pancake_Drop Pipe | Workshop | 4
 |  |  |  |  |  |  |  |  |  |  |  | M4 - Nyloc Nut | Nyloc Nut - M4 | TR Fastenings | 12
 |  |  |  |  |  |  |  |  |  |  |  | M4 x 16 - Socket Csk Screw (A2) | Socket Csk Screw - (A2) - M4 x 16 | TR Fastenings | 8
 |  |  |  |  |  |  |  | BSM.004.004 | Pancake_Exit Assy | Workshop | 1 | BSM.004.100 | Pancake_Angle Bracket 2 | Workshop | 2
 |  |  |  |  |  |  |  |  |  |  |  | BSM.004.109 | Pancake_Exit Board | Workshop | 1
 |  |  |  |  |  |  |  |  |  |  |  | BSM.004.110 | Pancake_Exit Piece | Workshop | 8
 |  |  |  |  |  |  |  |  |  |  |  | M4 - Nyloc Nut | Nyloc Nut - M4 | TR Fastenings | 20
 |  |  |  |  |  |  |  |  |  |  |  | M4 x 12 - Socket Csk Screw (A2) | Socket Csk Screw - (A2) - M4 x 12 | TR Fastenings | 4
 |  |  |  |  |  |  |  |  |  |  |  | M4 x 16 - Socket Csk Screw (A2) | Socket Csk Screw - (A2) - M4 x 16 | TR Fastenings | 16
 |  |  |  |  |  |  |  | BSM.004.005 | Pancake_Flexi Pipe Assy Flipped | Workshop | 1 | 451233010040020 | Socket Csk Screw - (A2) - M4 x 20 | TR Fastenings | 2
 |  |  |  |  |  |  |  |  |  |  |  | BSM.004.111 | Pancake_Flexi Pipe Flipped | Workshop | 1
 |  |  |  |  |  |  |  |  |  |  |  | BSM.004.112 | Pancake_Flexi Pipe Mount 2 | Workshop | 1
 |  |  |  |  |  |  |  |  |  |  |  | M4 - Nyloc Nut | Nyloc Nut - M4 | TR Fastenings | 2
 |  |  |  |  |  |  |  |  |  |  |  | M4 x 12 - Socket Csk Screw (A2) | Socket Csk Screw - (A2) - M4 x 12 | TR Fastenings | 2
 |  |  |  |  |  |  |  | BSM.004.006 | Pancake_Flexi Pipe Assy | Workshop | 1 | 451233010040020 | Socket Csk Screw - (A2) - M4 x 20 | TR Fastenings | 2
 |  |  |  |  |  |  |  |  |  |  |  | BSM.004.113 | Pancake_Flexi Pipe Mount | Workshop | 1
 |  |  |  |  |  |  |  |  |  |  |  | BSM.004.114 | Pancake_Flexi Pipe | Workshop | 1
 |  |  |  |  |  |  |  |  |  |  |  | M4 - Nyloc Nut | Nyloc Nut - M4 | TR Fastenings | 2
 |  |  |  |  |  |  |  |  |  |  |  | M4 x 12 - Socket Csk Screw (A2) | Socket Csk Screw - (A2) - M4 x 12 | TR Fastenings | 2
 |  |  |  |  |  |  |  | BSM.004.007 | Pancake_Reverse Assy | Workshop | 1 | 450712010040016 | Socket Cap Screw - Standard - (A2) - M4 x 16 | TR Fastenings | 4
 |  |  |  |  |  |  |  |  |  |  |  | 451233010030010 | Socket Csk Screw - (A2) - M3 x 10 | TR Fastenings | 21
 |  |  |  |  |  |  |  |  |  |  |  | BSM.004.101 | Pancake_Angle Bracket | Workshop | 4
 |  |  |  |  |  |  |  |  |  |  |  | BSM.004.102 | Pancake_Bearing | Workshop | 10
 |  |  |  |  |  |  |  |  |  |  |  | BSM.004.106 | Pancake_Connector | Workshop | 2
 |  |  |  |  |  |  |  |  |  |  |  | BSM.004.116 | Pancake_Floor Piece | Workshop | 4
 |  |  |  |  |  |  |  |  |  |  |  | BSM.004.127 | Pancake_Reverse Backboard 2 | Workshop | 1
 |  |  |  |  |  |  |  |  |  |  |  | BSM.004.128 | Pancake_Reverse Backboard | Workshop | 1
 |  |  |  |  |  |  |  |  |  |  |  | BSM.004.129 | Pancake_Reverse Lever | Workshop | 5
 |  |  |  |  |  |  |  |  |  |  |  | BSM.004.130 | Pancake_Reverse Shaft | Workshop | 5
 |  |  |  |  |  |  |  |  |  |  |  | BSM.004.131 | Pancake_Reverse Weight | Workshop | 5
 |  |  |  |  |  |  |  |  |  |  |  | circlip-6-bs-3673 | External Circlip | TR Fastenings | 5
 |  |  |  |  |  |  |  |  |  |  |  | FWSRS-D12-V4.5-E2.5-T3 | Countersunk Clamp Washer | TR Fastenings | 4
 |  |  |  |  |  |  |  |  |  |  |  | M3 x 12 - Socket Cap Screw - Standard (A2) | Socket Cap Screw - Standard - (A2) - M3 x 12 | TR Fastenings | 4
 |  |  |  |  |  |  |  |  |  |  |  | M4 - Nyloc Nut | Nyloc Nut - M4 | TR Fastenings | 16
 |  |  |  |  |  |  |  |  |  |  |  | M4 x 12 - Socket Csk Screw (A2) | Socket Csk Screw - (A2) - M4 x 12 | TR Fastenings | 8
 |  |  |  |  |  |  |  |  |  |  |  | M4 x 16 - Socket Csk Screw (A2) | Socket Csk Screw - (A2) - M4 x 16 | TR Fastenings | 4
 |  |  |  |  |  |  |  |  |  |  |  | nut_din_985-m3x0_5-8 | M3 Locknut | TR Fastenings | 5
 |  |  |  |  |  |  |  | BSM.004.008 | Pancake_Tilted Tube Assy 2 | Workshop | 1 | 450712010040016 | Socket Cap Screw - Standard - (A2) - M4 x 16 | TR Fastenings | 4
 |  |  |  |  |  |  |  |  |  |  |  | BSM.004.101 | Pancake_Angle Bracket | Workshop | 2
 |  |  |  |  |  |  |  |  |  |  |  | BSM.004.140 | Pancake_Tilt Pipe | Workshop | 1
 |  |  |  |  |  |  |  |  |  |  |  | BSM.004.141 | Pancake_Tilted Tube Backboard Long | Workshop | 1
 |  |  |  |  |  |  |  |  |  |  |  | M4 - Nyloc Nut | Nyloc Nut - M4 | TR Fastenings | 11
 |  |  |  |  |  |  |  |  |  |  |  | M4 x 12 - Socket Csk Screw (A2) | Socket Csk Screw - (A2) - M4 x 12 | TR Fastenings | 4
 |  |  |  |  |  |  |  |  |  |  |  | M4 x 16 - Socket Csk Screw (A2) | Socket Csk Screw - (A2) - M4 x 16 | TR Fastenings | 3
 |  |  |  |  |  |  |  | BSM.004.009 | Pancake_Tilted Tube Assy | Workshop | 1 | 450712010040016 | Socket Cap Screw - Standard - (A2) - M4 x 16 | TR Fastenings | 4
 |  |  |  |  |  |  |  |  |  |  |  | BSM.004.101 | Pancake_Angle Bracket | Workshop | 2
 |  |  |  |  |  |  |  |  |  |  |  | BSM.004.140 | Pancake_Tilt Pipe | Workshop | 1
 |  |  |  |  |  |  |  |  |  |  |  | BSM.004.142 | Pancake_Tilted Tube Backboard | Workshop | 1
 |  |  |  |  |  |  |  |  |  |  |  | M4 - Nyloc Nut | Nyloc Nut - M4 | TR Fastenings | 11
 |  |  |  |  |  |  |  |  |  |  |  | M4 x 12 - Socket Csk Screw (A2) | Socket Csk Screw - (A2) - M4 x 12 | TR Fastenings | 4
 |  |  |  |  |  |  |  |  |  |  |  | M4 x 16 - Socket Csk Screw (A2) | Socket Csk Screw - (A2) - M4 x 16 | TR Fastenings | 3
 |  |  |  |  |  |  |  | BSM.004.010 | Pancake_Timing Assy 2 | Workshop | 1 | 450712010040016 | Socket Cap Screw - Standard - (A2) - M4 x 16 | TR Fastenings | 10
 |  |  |  |  |  |  |  |  |  |  |  | BSM.004.012 | Pancake_Timing Assy_Lever Shaft 2 | Workshop | 1 | BSM.003.103 | Timing_Lever Weight | Workshop | 5
 |  |  |  |  |  |  |  |  |  |  |  |  |  |  |  | BSM.004.118 | Pancake_Lever Shaft 2 | Workshop | 1
 |  |  |  |  |  |  |  |  |  |  |  |  |  |  |  | BSM.004.121 | Pancake_Lever | Workshop | 5
 |  |  |  |  |  |  |  |  |  |  |  |  |  |  |  | circlip-6-bs-3673 | External Circlip | TR Fastenings | 12
 |  |  |  |  |  |  |  |  |  |  |  |  |  |  |  | M3 x 0.5mm Zinc Plated Steel Washer | M3 Washer | TR Fastenings | 5
 |  |  |  |  |  |  |  |  |  |  |  |  |  |  |  | M3 x 10 - Socket Button Head (A2) | Socket Button Head - (A2) - M3 x 10 | TR Fastenings | 5
 |  |  |  |  |  |  |  |  |  |  |  | BSM.004.014 | Pancake_Timing Assy_Star Shaft 2 | Workshop | 1 | BSM.003.107 | Timing_Star | Workshop | 5
 |  |  |  |  |  |  |  |  |  |  |  |  |  |  |  | BSM.004.136 | Pancake_Star Shaft 2 | Workshop | 1
 |  |  |  |  |  |  |  |  |  |  |  |  |  |  |  | circlip-6-bs-3673 | External Circlip | TR Fastenings | 7
 |  |  |  |  |  |  |  |  |  |  |  |  |  |  |  | M3 x 12 - Socket Cap Screw - Standard (A2) | Socket Cap Screw - Standard - (A2) - M3 x 12 | TR Fastenings | 4
 |  |  |  |  |  |  |  |  |  |  |  |  |  |  |  | nut_din_985-m3x0_5-8 | M3 Locknut | TR Fastenings | 4
 |  |  |  |  |  |  |  |  |  |  |  |  |  |  |  | SAFL212 | Oval 2 Bolt Flanged Unit | acorn | 2
 |  |  |  |  |  |  |  |  |  |  |  | BSM.004.101 | Pancake_Angle Bracket | Workshop | 2
 |  |  |  |  |  |  |  |  |  |  |  | BSM.004.103 | Pancake_Bracket | Workshop | 2
 |  |  |  |  |  |  |  |  |  |  |  | BSM.004.124 | Pancake_PVC Pipe 2 | Workshop | 5
 |  |  |  |  |  |  |  |  |  |  |  | BSM.004.143 | Pancake_Timing Backboard 2 | Workshop | 1
 |  |  |  |  |  |  |  |  |  |  |  | FWSRS-D12-V4.5-E2.5-T3 | Countersunk Clamp Washer | TR Fastenings | 2
 |  |  |  |  |  |  |  |  |  |  |  | M4 - Nyloc Nut | Nyloc Nut - M4 | TR Fastenings | 22
 |  |  |  |  |  |  |  |  |  |  |  | M4 x 16 - Socket Csk Screw (A2) | Socket Csk Screw - (A2) - M4 x 16 | TR Fastenings | 12
 |  |  |  |  |  |  |  | BSM.004.011 | Pancake_Timing Assy | Workshop | 1 | 450712010040016 | Socket Cap Screw - Standard - (A2) - M4 x 16 | TR Fastenings | 4
 |  |  |  |  |  |  |  |  |  |  |  | BSM.004.013 | Pancake_Timing Assy_Lever Shaft | Workshop | 1 | BSM.003.104 | Timing_Lever | Workshop | 10
 |  |  |  |  |  |  |  |  |  |  |  |  |  |  |  | BSM.004.119 | Pancake_Lever Shaft | Workshop | 1
 |  |  |  |  |  |  |  |  |  |  |  |  |  |  |  | BSM.004.120 | Pancake_Lever Weight | Workshop | 5
 |  |  |  |  |  |  |  |  |  |  |  |  |  |  |  | BSM.004.138 | Pancake_Switch Lever 2 | Workshop | 4
 |  |  |  |  |  |  |  |  |  |  |  |  |  |  |  | circlip-6-bs-3673 | External Circlip | TR Fastenings | 28
 |  |  |  |  |  |  |  |  |  |  |  |  |  |  |  | M3 x 0.5mm Zinc Plated Steel Washer | M3 Washer | TR Fastenings | 10
 |  |  |  |  |  |  |  |  |  |  |  |  |  |  |  | M3 x 10 - Socket Button Head (A2) | Socket Button Head - (A2) - M3 x 10 | TR Fastenings | 10
 |  |  |  |  |  |  |  |  |  |  |  | BSM.004.015 | Pancake_Timing Assy_Star Shaft | Workshop | 1 | BSM.003.107 | Timing_Star | Workshop | 10
 |  |  |  |  |  |  |  |  |  |  |  |  |  |  |  | BSM.004.137 | Pancake_Star Shaft | Workshop | 1
 |  |  |  |  |  |  |  |  |  |  |  |  |  |  |  | circlip-6-bs-3673 | External Circlip | TR Fastenings | 12
 |  |  |  |  |  |  |  |  |  |  |  |  |  |  |  | SAFL212 | Oval 2 Bolt Flanged Unit | acorn | 2
 |  |  |  |  |  |  |  |  |  |  |  | BSM.004.101 | Pancake_Angle Bracket | Workshop | 2
 |  |  |  |  |  |  |  |  |  |  |  | BSM.004.125 | Pancake_PVC Pipe Long | Workshop | 5
 |  |  |  |  |  |  |  |  |  |  |  | BSM.004.126 | Pancake_PVC Pipe | Workshop | 5
 |  |  |  |  |  |  |  |  |  |  |  | BSM.004.144 | Pancake_Timing Backboard | Workshop | 1
 |  |  |  |  |  |  |  |  |  |  |  | M4 - Nyloc Nut | Nyloc Nut - M4 | TR Fastenings | 24
 |  |  |  |  |  |  |  |  |  |  |  | M4 x 16 - Socket Csk Screw (A2) | Socket Csk Screw - (A2) - M4 x 16 | TR Fastenings | 20
 |  |  |  |  |  |  |  | BSM.004.016 | Pancake_Top Board Assy | Workshop | 1 | 451233010030010 | Socket Csk Screw - (A2) - M3 x 10 | TR Fastenings | 4
 |  |  |  |  |  |  |  |  |  |  |  | 451233010040020 | Socket Csk Screw - (A2) - M4 x 20 | TR Fastenings | 10
 |  |  |  |  |  |  |  |  |  |  |  | BSM.002.115 | Selection_Washer | Workshop | 4
 |  |  |  |  |  |  |  |  |  |  |  | BSM.004.100 | Pancake_Angle Bracket 2 | Workshop | 2
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

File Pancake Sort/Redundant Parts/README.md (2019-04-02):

## Redundant Parts

Components previously designed but no longer used.

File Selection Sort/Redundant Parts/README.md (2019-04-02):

# Redundant Parts

Components previously designed but no longer used.

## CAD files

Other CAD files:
Pancake Sort/Pancake - 3 Lanes/BSM.012.010 - Pancake_Timing Assy 2_3 Lanes.dwg
Pancake Sort/Pancake - 4 Lanes/BSM.011.010 - Pancake_Timing Assy 2_4 Lanes.dwg
Selection Sort/Selection - 2 Lanes/BSM.010.002 - Selection_Exit Pipe Assy 2 Lanes.dwg
Selection Sort/Selection - 2 Lanes/Redundant parts/BSM.010.005 - Selection_Exit Pipe Assy Long 2 Lanes.dwg
Selection Sort/Selection - 3 Lanes/BSM.009.001 - Selection_Assy 3 Lanes.dwg
Selection Sort/Selection - 4 Lanes/BSM.008.001 - Selection_Assy 4 Lanes.dwg
Pancake Sort/Pancake - 3 Lanes/BSM.012.011 - Pancake_Timing Assy_3 Lanes.dwg
Selection Sort/Selection - 2 Lanes/BSM.010.001 - Selection_Assy 2 Lanes.dwg
Selection Sort/Selection - 3 Lanes/BSM.009.005 - Selection_Exit Pipe Assy Long 3 Lanes.dwg
Selection Sort/Selection - 4 Lanes/BSM.008.002 - Selection_Exit Pipe Assy 4 Lanes.dwg
Top Level/BSM.001.003 - Top_Lever Assy.dwg
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

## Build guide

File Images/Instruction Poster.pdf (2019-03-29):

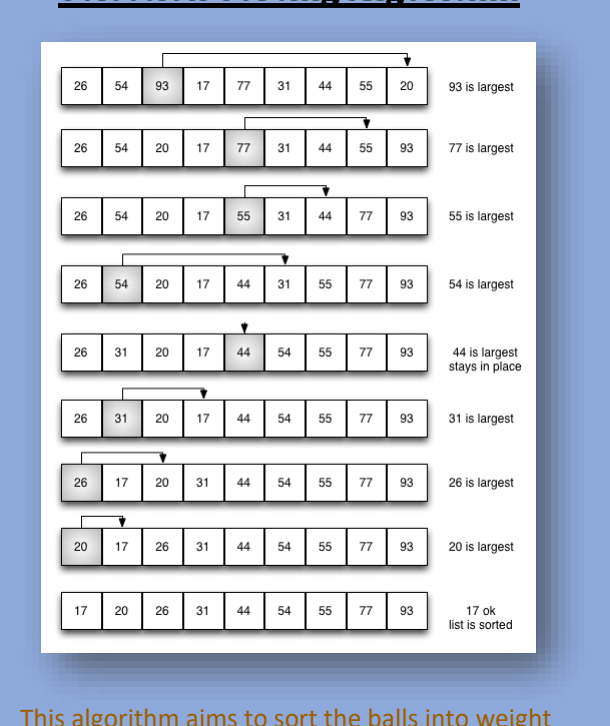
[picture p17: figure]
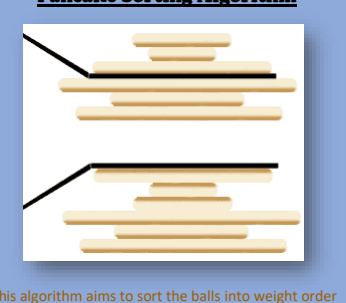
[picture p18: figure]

Designer: James Taylor | https://github.com/jamesrussellt/Ball-Machine

Selection Sorting Algorithm

This algorithm aims to sort the balls into weight order in the least number of comparisons possible.

The largest number (or in our case, the heaviest ball) is selected and moved to the right. This process repeats until the numbers (or balls) are in order.

Pancake Sorting Algorithm

This algorithm aims to sort the balls into weight order in the least number of reversals (or pancake flips) possible.

Imagine you have a stack of pancakes (heavier balls = larger pancakes) and the only way of moving them is by inserting your spatula and flipping all pancakes on top of it.

After identifying the largest pancake (using the selection sorting algorithm), the spatula is inserted and flips that section of the pile so that the largest pancake (heaviest ball) is at the top of the pile. The spatula is inserted at the bottom of the pile and flips the whole pile so the largest pancake (heaviest ball) now ends up at the bottom.

This process repeats until the pancakes are in size order.

# Ball Sorting Machine

Instructions

- Turn lever UP to sort balls using Selection Sorting Algorithm
- Turn lever DOWN to sort balls using Pancake Sorting Algorithm
- Place all balls in top of machine, one ball per lane

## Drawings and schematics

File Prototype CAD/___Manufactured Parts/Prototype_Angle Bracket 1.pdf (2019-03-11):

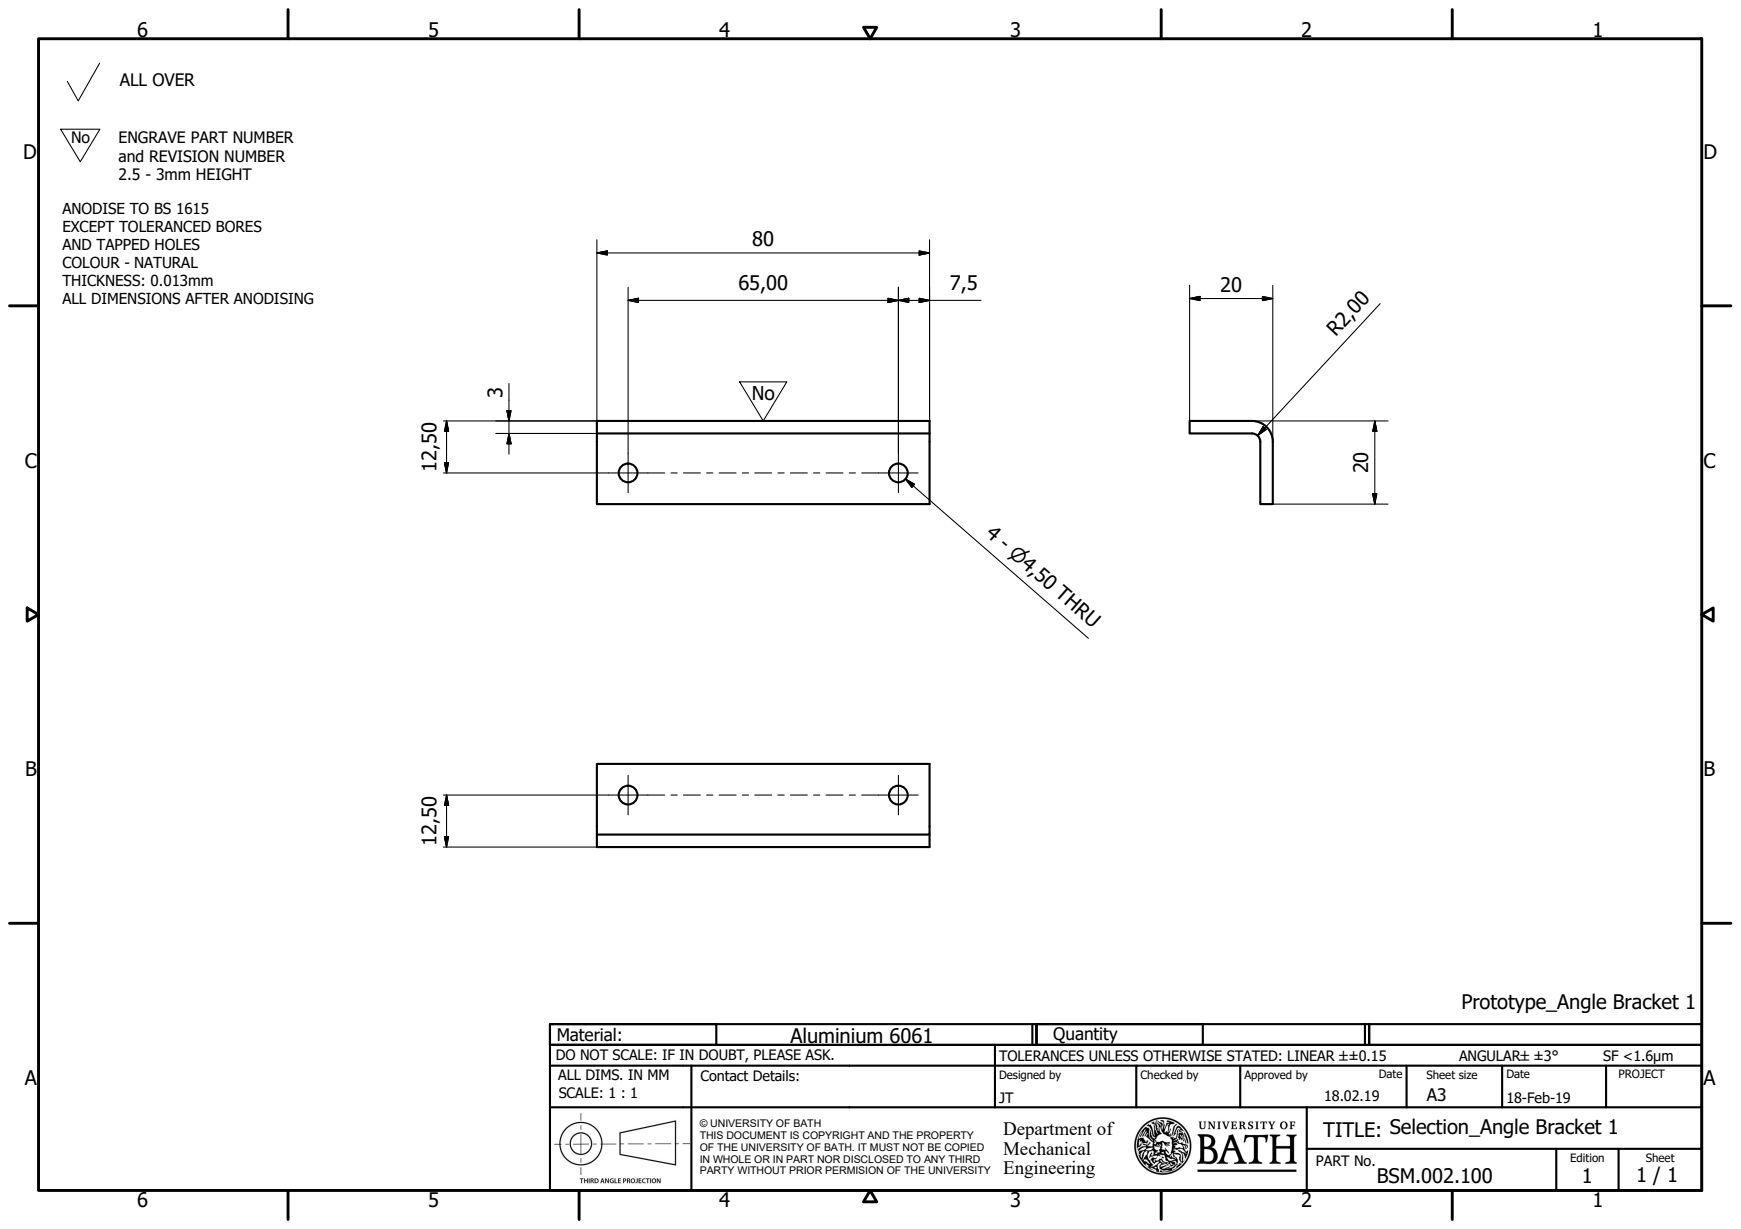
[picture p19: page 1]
ALL OVER; Prototype_Angle Bracket 1

ENGRAVE PART NUMBER
and REVISION NUMBER
2.5 - 3mm HEIGHT

ANODISE TO BS 1615
EXCEPT TOLERANCED BORES
AND TAPPED HOLES
COLOUR -
THICKNESS: 0.013mm
ALL DIMENSIONS AFTER ANODISING

Material: | Aluminium 6061 | Quantity
DO NOT SCALE: IF IN DOUBT, PLEASE ASK. | TOLERANCES UNLESS OTHERWISE STATED: LINEAR ±0.15 ANGULAR±3° SF <1.6µm
ALL DIMS. IN MM SCALE: 1 : 1 | | Contact Details: | Designed by JT | Checked by | Approved by Date 18.02.19 | Sheet size A3 | Date 18-Feb-19 | PROJECT

© UNIVERSITY OF BATH THIS DOCUMENT IS COPYRIGHT AND THE PROPERTY OF THE UNIVERSITY OF BATH. IT MUST NOT BE COPIED IN WHOLE OR IN PART NOR DISCLOSED TO ANY THIRD PARTY WITHOUT PRIOR PERMISION OF THE UNIVERSITY | Department of Mechanical Engineering | Selection_Angle Bracket 1 TITLE:

PART No. BSM.002.100 | Edition 1 | Sheet 1 / 1

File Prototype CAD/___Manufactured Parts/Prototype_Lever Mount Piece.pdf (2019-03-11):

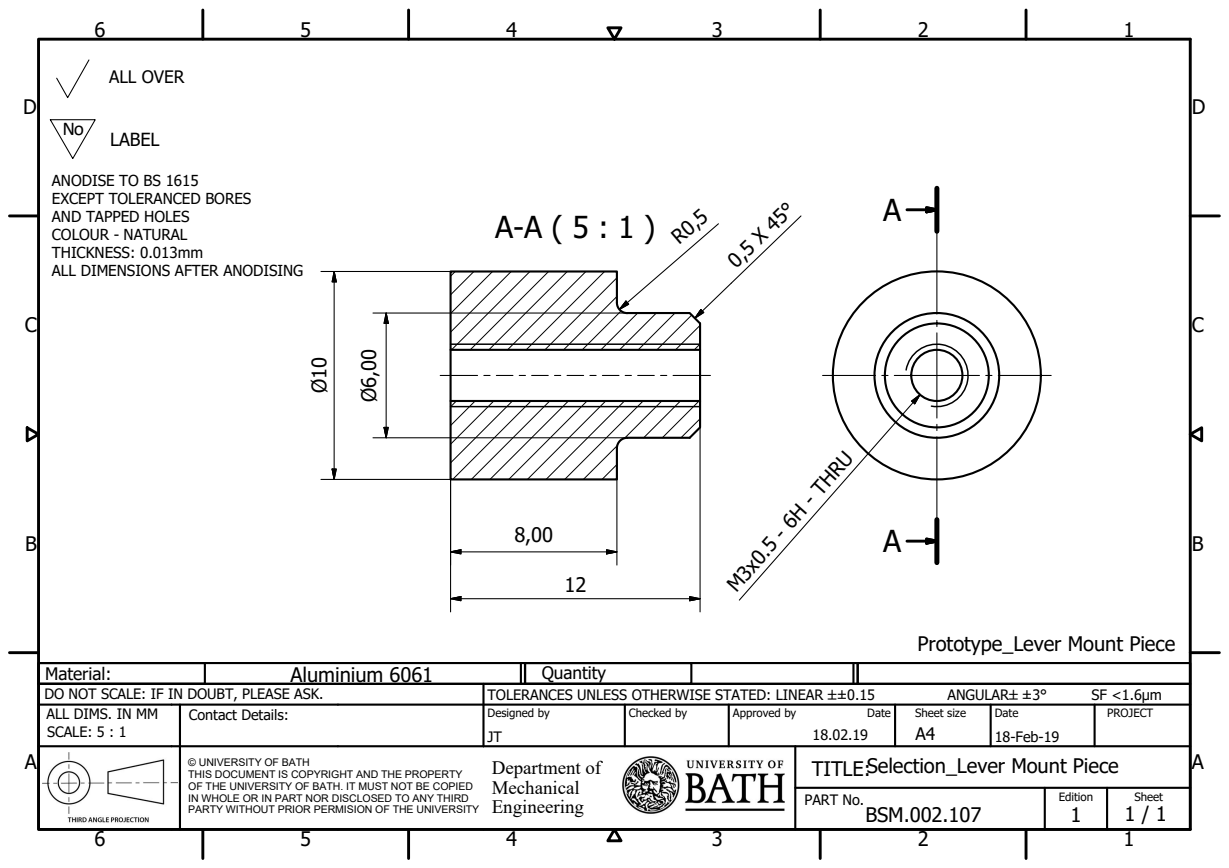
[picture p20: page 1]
ALL OVER; M3x0.5 - 6H - THRU; Prototype_Lever Mount Piece

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

Material: | Aluminium 6061 | Quantity
DO NOT SCALE: IF IN DOUBT, PLEASE ASK. | TOLERANCES UNLESS OTHERWISE STATED: LINEAR ±0.15 ANGULAR±3° SF <1.6µm
ALL DIMS. IN MM SCALE: 5 : 1 | | Contact Details: | Designed by JT | Checked by | Approved by Date 18.02.19 | Sheet size A4 | Date 18-Feb-19 | PROJECT

© UNIVERSITY OF BATH THIS DOCUMENT IS COPYRIGHT AND THE PROPERTY OF THE UNIVERSITY OF BATH. IT MUST NOT BE COPIED IN WHOLE OR IN PART NOR DISCLOSED TO ANY THIRD PARTY WITHOUT PRIOR PERMISION OF THE UNIVERSITY | Department of Mechanical Engineering | TITLE: Selection_Lever Mount Piece

PART No. BSM.002.107 | Edition 1 | Sheet 1 / 1

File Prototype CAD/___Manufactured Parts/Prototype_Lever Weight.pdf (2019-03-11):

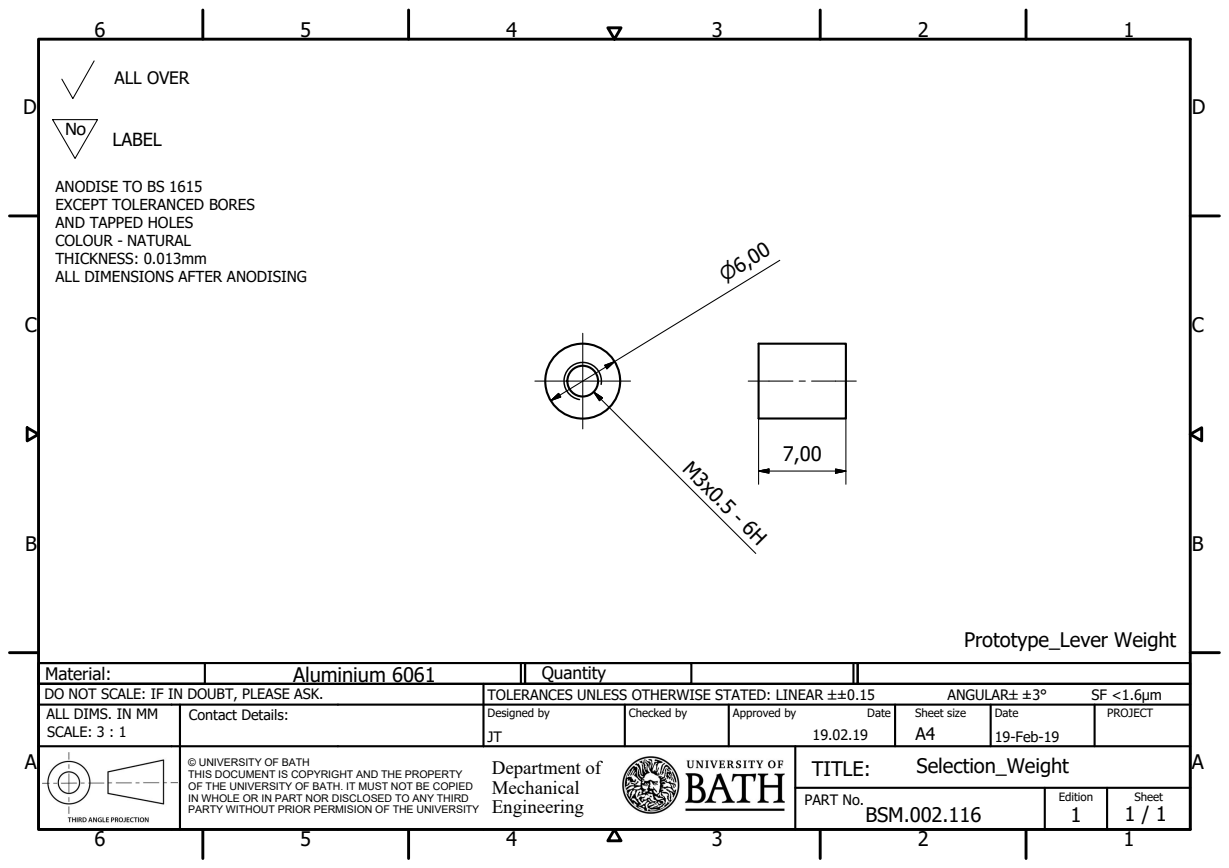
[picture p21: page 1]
ALL OVER; Prototype_Lever Weight

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

Material: | Aluminium 6061 | Quantity
DO NOT SCALE: IF IN DOUBT, PLEASE ASK. | TOLERANCES UNLESS OTHERWISE STATED: LINEAR ±0.15 ANGULAR±3° SF <1.6µm
ALL DIMS. IN MM SCALE: 3 : 1 | | Contact Details: | Designed by JT | Checked by | Approved by Date 19.02.19 | Sheet size A4 | Date 19-Feb-19 | PROJECT

© UNIVERSITY OF BATH THIS DOCUMENT IS COPYRIGHT AND THE PROPERTY OF THE UNIVERSITY OF BATH. IT MUST NOT BE COPIED IN WHOLE OR IN PART NOR DISCLOSED TO ANY THIRD PARTY WITHOUT PRIOR PERMISION OF THE UNIVERSITY | Department of Mechanical Engineering | Selection_Weight TITLE:

PART No. BSM.002.116 | Edition 1 | Sheet 1 / 1

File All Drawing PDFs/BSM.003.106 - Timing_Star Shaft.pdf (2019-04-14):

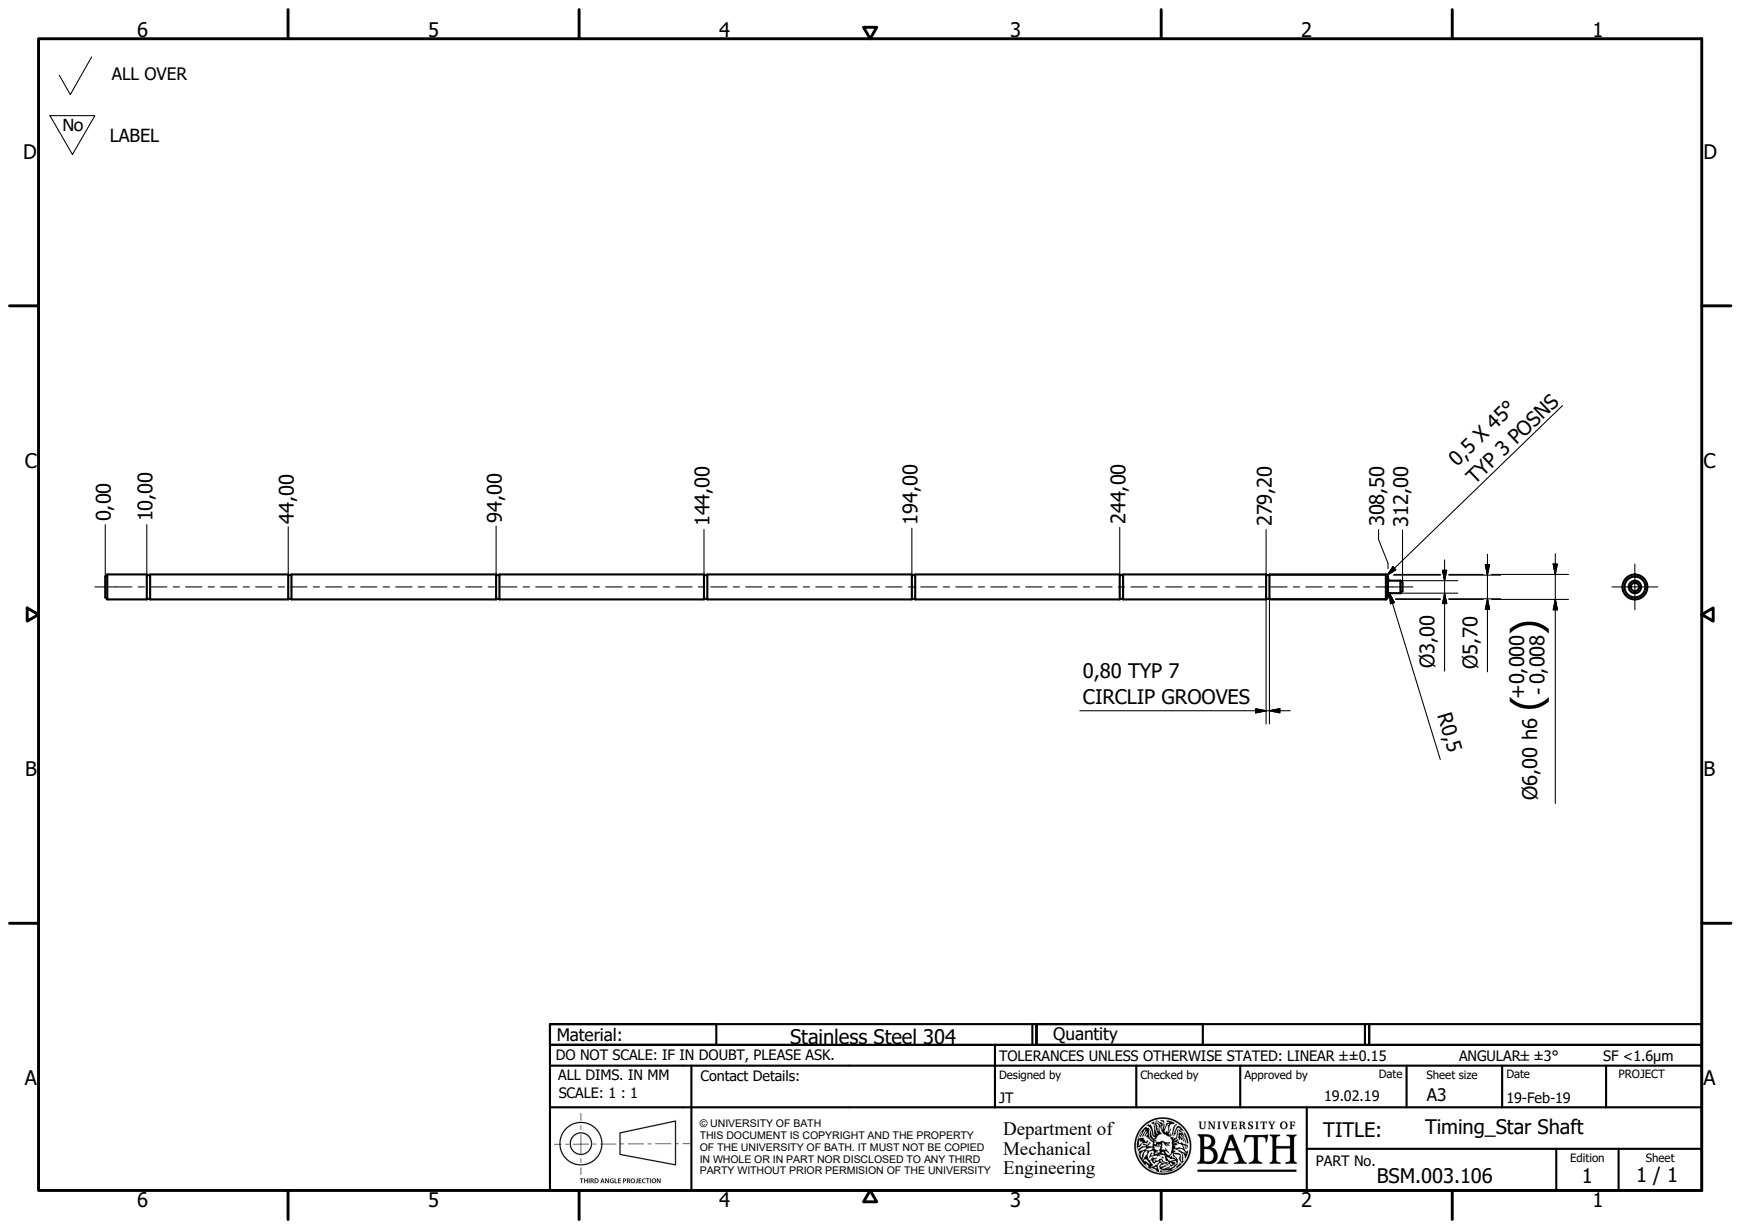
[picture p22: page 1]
ALL OVER; 0,80 TYP 7 CIRCLIP GROOVES; TYP 3 POSNS

Material: | Stainless Steel 304 | Quantity
DO NOT SCALE: IF IN DOUBT, PLEASE ASK. | TOLERANCES UNLESS OTHERWISE STATED: LINEAR ±0.15 ANGULAR±3° SF <1.6µm
ALL DIMS. IN MM SCALE: 1 : 1 | | Contact Details: | Designed by JT | Checked by | Approved by Date 19.02.19 | Sheet size A3 | Date 19-Feb-19 | PROJECT

© UNIVERSITY OF BATH THIS DOCUMENT IS COPYRIGHT AND THE PROPERTY OF THE UNIVERSITY OF BATH. IT MUST NOT BE COPIED IN WHOLE OR IN PART NOR DISCLOSED TO ANY THIRD PARTY WITHOUT PRIOR PERMISION OF THE UNIVERSITY | Department of Mechanical Engineering | Timing_Star Shaft TITLE:

PART No. BSM.003.106 | Edition 1 | Sheet 1 / 1

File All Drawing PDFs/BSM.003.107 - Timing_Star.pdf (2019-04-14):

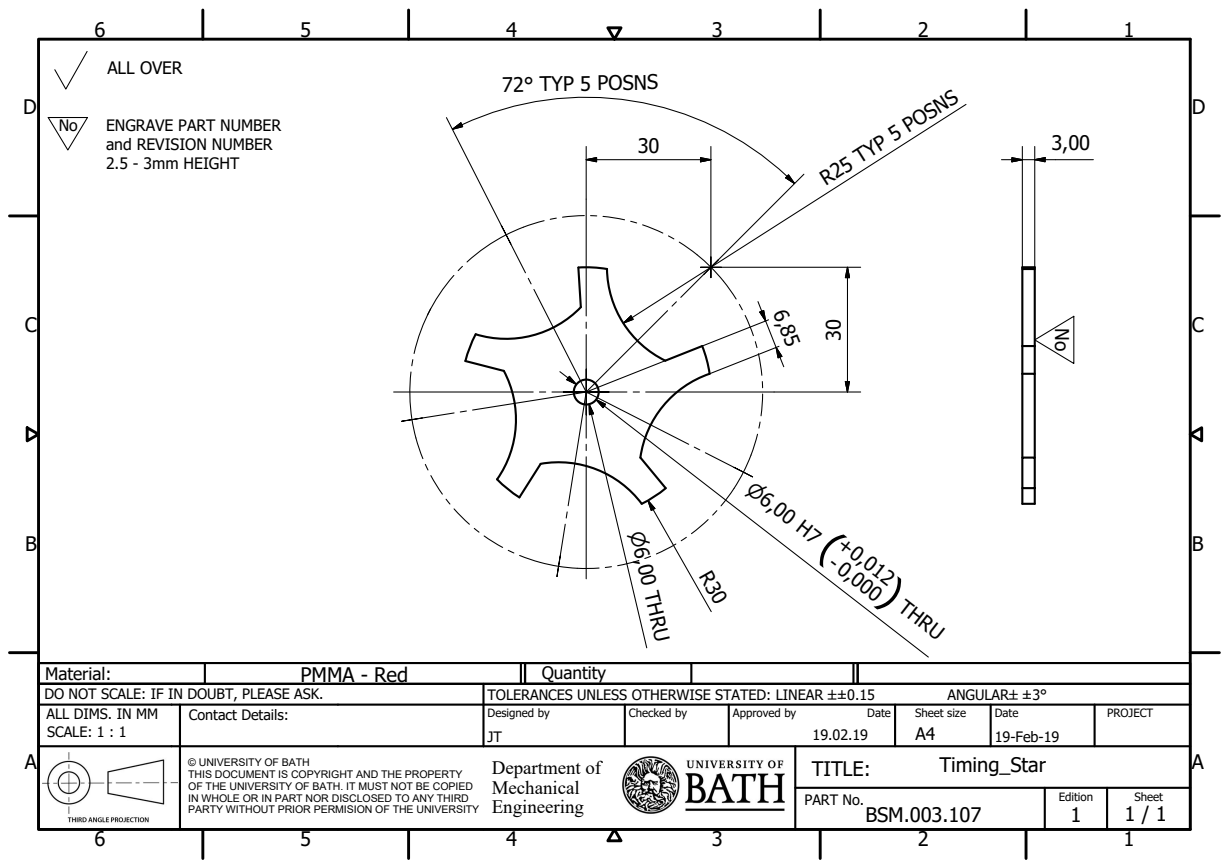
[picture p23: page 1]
ALL OVER; R25 TYP 5 POSNS; 72° TYP 5 POSNS; ) THRU

ENGRAVE PART NUMBER
and REVISION NUMBER
2.5 - 3mm HEIGHT

Material: | PMMA - Red | Quantity
DO NOT SCALE: IF IN DOUBT, PLEASE ASK. | TOLERANCES UNLESS OTHERWISE STATED: LINEAR ±0.15 ANGULAR±3°
ALL DIMS. IN MM SCALE: 1 : 1 | | Contact Details: | Designed by JT | Checked by | Approved by Date 19.02.19 | Sheet size A4 | Date 19-Feb-19 | PROJECT

© UNIVERSITY OF BATH THIS DOCUMENT IS COPYRIGHT AND THE PROPERTY OF THE UNIVERSITY OF BATH. IT MUST NOT BE COPIED IN WHOLE OR IN PART NOR DISCLOSED TO ANY THIRD PARTY WITHOUT PRIOR PERMISION OF THE UNIVERSITY | Department of Mechanical Engineering | Timing_Star TITLE:

PART No. BSM.003.107 | Edition 1 | Sheet 1 / 1

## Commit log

2019-03-11 Moving from other repository
    [BS 3673 - 6mm External Circlip.0002.ipt, BS 3673 - 6mm External Circlip.ipt, BSM.002.001 - Selection_Assy.0018.dwg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]
2019-03-12 Drawing Update
    [BSM.002.001 - Selection_Assy.0018.dwg, BSM.002.001 - Selection_Assy.0019.dwg, BSM.002.001 - Selection_Assy.dwg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]
2019-03-18 Update top
    [BSM.002.001 - Selection_Assy.0020.dwg, BSM.002.001 - Selection_Assy.0021.dwg, BSM.002.001 - Selection_Assy.dwg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]
2019-03-18 Update Top Assy
    [BSM.004.001 - Pancake_Assy.0009.dwg, BSM.004.001 - Pancake_Assy.0010.dwg, BSM.004.001 - Pancake_Assy.dwg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]
2019-04-09 PDF pack Update
    [BSM.001.002 - Top_Backboard Assy.0004.dwg, BSM.001.002 - Top_Backboard Assy.0005.dwg, BSM.001.002 - Top_Backboard Assy.dwg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]
